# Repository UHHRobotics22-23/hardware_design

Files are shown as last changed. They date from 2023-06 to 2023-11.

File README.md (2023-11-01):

# Hardware Design
This repository contains the design files associated with the hardware mallet holder.
Further the firmware employed on the micro controller and a supporting calibration procedure script is contained.

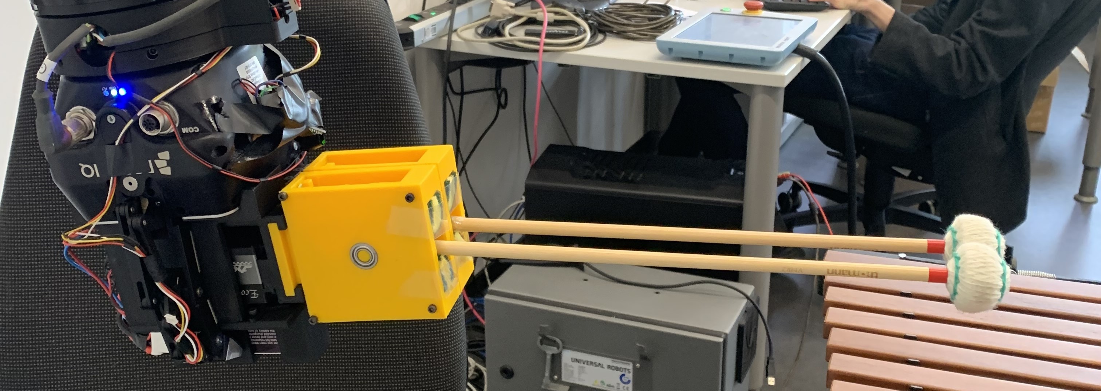
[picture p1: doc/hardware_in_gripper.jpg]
The mallet holder assembly in the gripper of the UR5

*The mallet holder assembly in the gripper of the UR5*

## Hardware Model Design
[OpenSCAD](https://openscad.org/) was used for the design of the 3D printable models.
Generally the designs can be separated into one and two mallet design, where the one mallet designs were the basis for the two mallet approaches.
All designs were created to be used in the [three finger gripper](https://robotiq.com/products/3-finger-adaptive-robot-gripper) employed as the end effector of the UR5.

### Two Mallet Designs
The two mallet designs are split into two categories, the servo controlled element and the attachments.
The servo controlled element contains all electronics and two mounting points for an attachment making the design more modular.
The attachments were then mounting the mallets, either with or without compliance.
#### Servo Controlled Element
All servo controlled elements have a standard "claw" element which the attachment modules can be slotted in to.

The first version of the servo controlled element [double_mallet_servo](design/two_mallet/double_mallet_servo/double_mallet_servo.scad) mainly tested the servo based control for the second mallet and the attachment mount.
[double_mallet_servo_compliant_full](design/two_mallet/double_mallet_servo/double_mallet_servo_compliant_full.scad) was used to generated STL models for a first URDF file with the [double_flex_v2](design/two_mallet/modular_attachments/double_flex_v2.scad) included.
Later versions were created in a more modular fashion.

[double_mallet_servo_UR5](design/two_mallet/double_mallet_servo/double_mallet_servo_UR5.scad) is the second iteration of the element. The length of the part was increased to allow the gripper to grab the device from the top.
Further the control and power electronics could be added to the back.
The top plate was changed to have indexing ridges to the gripper end effector of the UR5.
The [double_mallet_servo_UR5_battery](design/two_mallet/double_mallet_servo/double_mallet_servo_UR5_battery.scad) added a battery holder for the 2s lipo to the bottom plate.

#### Attachments
Three attachment design files exist for the two mallet holder.
All designs feature a standardized attachment mechanism to be added to the servo controlled element.

First the [static_mallet_attachment](design/two_mallet/modular_attachments/static_mallet_attachment.scad) is a simple static holder without added compliance generally used for testing.

In the final version the [double_flex_v2](design/two_mallet/modular_attachments/double_flex_v2.scad) has been used. It is based on the [double_flex_v1](design/one_mallet/double_flex_v1/mallet_mount_double_flex_v1.scad) and as such allows for flexibility in both directions using rubber bands. Two additional pieces of sponge were added at the top and bottom to dampen the movements.

[double_flex_v2_collision](design/two_mallet/modular_attachments/double_flex_v2_collision.scad) was not used.

### One Mallet Designs
The [rigid_base_version](design/one_mallet/rigid_base_version/rigid.scad) is the design used for playing with only one mallet. It features a simple holder and grabbing points for the end effector.

To generate louder sounds a compliant approach was devised.

[v1](design/one_mallet/v1/mallet_mount_v1.scad) is the first compliant design, featuring a one directional, up compliance when hitting the instrument. The compliance is achieved with rubber bands. [v2](design/one_mallet/v2/mallet_mount_v2.scad) is a minor iteration on the design using bearings and felt stickers to reduce noise.

The [double_flex_v1](design/one_mallet/double_flex_v1/mallet_mount_double_flex_v1.scad) allowed compliance into the up and down direction which showed improvements in the loudness of the instrument.

## Firmware
The firmware is implemented using the [Arduino](https://www.arduino.cc/) framework.
A [Raspberry Pi Pico W](https://www.raspberrypi.com/documentation/microcontrollers/raspberry-pi-pico.html) is used as the controller of the device.

### Protocol
The protocol used for the communication between ROS and the microcontroller is based on simple string commands. For both the wifi and serial version the same protocol is used.
Commands for the serial version have to be \n terminated.
The wifi version accepts both with and without

At first the ROS side is expected to request the bounds and resolution using the "l" command.
This allows for multiple devices with different bound to be used interchangeably though it could also be realized with config parameters on the ROS side.

The "p" command is used in the read phase of the hardware_interface (See [marimbabot_hardware](https://github.com/UHHRobotics22-23/marimbabot/tree/main/marimbabot_hardware)).

Lastly the "s" command allows the ROS side to give a integer valued command position to the microcontroller.

| Command | Response | Command Description | Response Description |
|---|---|---|---|
| s \<value> | ok, err_input_num, err_input_range | Commands the servo to move to the value <value> | Errors for invalid number formats or numbers out of range of the safety limits or ok for acknowledgement |
| p | p \<value> | Requests the current target value | Returns the current target value <value> |
| l | l <min_val> <max_val> <val_resolution> | Requests the limits of the device | Return the max and min value bounds and the resolution of the value parameter (0-res) |
| <invalid_command> | err_cmd | Any command other than the listed ones | Error code for and invalid / unknown command |

### Flavours
Two firmwares were written as a part of the development process.
First one using a usb serial connection and secondly one using a wifi network created by the microcontroller.

Both firmwares feature the min and max value at the top of the file.
These are the max and min angle the servo can safely be set to and depends on the real world alignment of the servo and the 3d print.
The values for each device are found in a manual testing project by sending manual "s" commands.
The resolution for both is set to 180 as the servo can cover 180°
Alternatively the resolution could be increased by using direct the [pwm millisecond control mode](https://www.arduino.cc/reference/en/libraries/servo/writemicroseconds/).

#### Wifi
The wifi firmware is found in the [mallet_play_servo_wifi](arduino_code/mallet_play_servo_wifi/mallet_play_servo_wifi.ino) project.

The SSID and the password of the generated network can be set at the top of the file and needs reflashing.
Further the port of the UDP server can be adjusted inside of the setup function.

Currently the defaults are:  
SSID: **Marimbabot_Mallet**  
PWD: **12345678**  
PORT: **8888**

Additional Note: In the libraries for the Raspberry Pi Pico W we found the Servo library to behave in unexpected ways which required a doubling of the input value to achieve the actually requested angle.

#### Serial
The serial firmware is found in the [mallet_play_servo](arduino_code/mallet_play_servo/mallet_play_servo.ino) project.

In the serial firmware the update frequency can be adjusted by changing the delay at the end of the loop.
The baud rate can be adjusted in the setup function. A high baud rate is needed to minimize the communication overhead.

## Electronics Design
The system was designed to be fully portable and battery powered to enable the usage in differing robotic arms.
Further the main used arms power budget was not able to power the device as the  end effector gripper exhausted this.

List of parts:
- Servo: [JX Servo CLS6336HV](http://jx-servo.com/en/Product/CORELESS1/HVcs/480.html)
- Battery: [CHHL 2S 2200mAh 30C](https://chinahobbyline.com/collections/cnhl-voltage-7-4v-2s-lipo-batteries/products/cnhl-2200mah-7-4v-2s-30c-lipo-battery-with-t-plug)
- DC Step Down: [LM2596](https://www.az-delivery.de/en/products/lm2596s-dc-dc-step-down-modul-1)
- Microcontroller: [Raspberry Pi Pico W](https://www.raspberrypi.com/documentation/microcontrollers/raspberry-pi-pico.html)
- A safety diode preventing current running back from a USB 5V supply

The system uses a 2s LIPO as its power source.
The servo is directly powered by the battery.
For the Raspberry Pi Pico W can only accept input voltages up to 5.5V.
A step down converter was used to step the 6-8V of the battery to 5V to safely power the microcontroller.

The full wiring diagram is shown in the following figure


## Hardware Calibration
The hardware calibration scripts are found in the [hardware_calibration](hardware_calibration) folder. The calibration is done by using a Azure Kinect depth camera in combination of color separation to find the 3d position of the red tapes on the mallets. The 3d coordinates are used to find the distance between the elements.
A mathematical model of the two mallet assembly is then used to find the expected opening angle from the distance. This angle is then compared to the commanded angle.

### How to use
First install the python dependencies using the [requirements.txt](hardware_calibration/requirements.txt) found in the hardware_calibration folder.

#### Setup
Use the azure kinect depth camera and connect it to the computer. A top down orientation onto the two mallet assembly indicated the best results. Clean the space of other red elements or cover them (like the red cables on the assembly).
Connect the computer to the Wifi sent out by the mallet assembly (the scripts use the raw control commands).

#### Data Collection
Two scripts are used for the measurement process.

First start [hardware_calibration.py](hardware_calibration/hardware_calibration.py).
This script uses the depth camera to measure the distance of the red tapes on the mallet.
The results are logged into a timestamped csv file (f"calibration-{time.time()}.csv").

Secondly start the [calibration_process.py](hardware_calibration/calibration_process.py).
This will generate the control input to the mallet holder and log to timestamp of each command.
One full sweep is run.
The data it logged into a timestamped csv file (f"calibration_pos-{time()}.csv").

After the sweep stop both scripts.

#### Data Preparation
To prepare the results remove all distance measurements before the first command value.
The analysis expects a continuous numberization of the meassurements.
The measured distance file also warrants careful examinations as the depth camera seems to have a few areas with bad accuracy.

#### Data Analysis
The data is analyzed using the Jupyter notebook [analyse_results.ipynb](hardware_calibration/analyse_results.ipynb).
To add new measurements extend the range operator in the 5th cell and run the notebook.
Especially the last graph gives a result about the angular offset for each commanded angle.

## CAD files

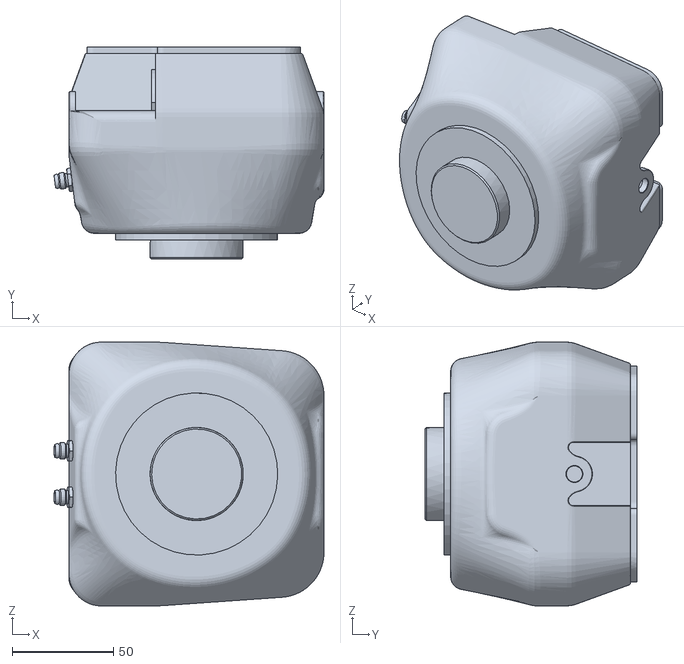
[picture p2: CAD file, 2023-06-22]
design/two_mallet/double_mallet_servo/palm_1.stl
133.2 x 104.8 x 130.2

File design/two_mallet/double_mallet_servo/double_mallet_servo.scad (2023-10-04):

/*
 * The first version of the two mallet holder servo controlled part
 */

$fa = 1;
$fs = 0.4;
/////////////////////////SERVO MODEL////////////////////////////
module servo(){
    color([0,0,1])
    difference (){
    union(){    
    rotate([90,0,90])//Servo Corpus
        cube([40, 39.5, 20]); 
        
    translate([0,40,8])//Screwholders
        cube([20,7.25,2.6]); 
    translate([0,-7.25,8])
        cube([20,7.25,2.6]);
    
    translate([10,10,-2]) //Drive shaft
        cylinder(h=3, r=6.5);
    translate([10,10,-5.5])
        cylinder(h=4, r=5.8/2);
        
    translate([10-3.5,-4.7,33])
        cube([7,8,5]);
        
    }
    ///////////Cutting///////////
    
    union(){ //Cut out Screwholes
    screwholes_servo();
    translate([20,40,0])
    rotate([0,0,180])
    screwholes_servo();
    }
}
  
}

// Screw Holder for connecting the servo
module screwholes_servo(){
     translate([0, 0, 7.9]) {
        translate([5, -7.25/2, 0]){
            cylinder(h=3, r=4.4/2);
            translate([-1.8,-4.8,0])
            cube([3.6, 4, 3]); 
        }
           translate([15, -7.25/2, 0]){
            cylinder(h=3, r=4.4/2);
            translate([-1.8,-4.8,0])
            cube([3.6, 4, 3]); 
        }
      
    }
}

// Module model for the drive shaft cross attachment used from the servo kit
module drive_shaft_attachment(){
    translate([-19,-19,0]){
        difference(){
            union(){
            
             translate([0,14.5,0])
                cube([38, 9, 2.77]); 
             translate([14.5,0,0])
                cube([9, 38, 2.77]); 
            translate([19,19,0])
                cylinder(h=5.4, r=4.4);   
                }
             union(){   
             translate([19,19,-00.1])//Driftshaft Clutch
                cylinder(h=6, r=5.8/2);
             translate([6,19,-00.1]) //Screwhole
                 cylinder(h=30, r=3/2);
              translate([32,19,-00.1])//Screwhole
                 cylinder(h=30, r=3/2);
              translate([19,32,-00.1])//Screwhole
                 cylinder(h=30, r=3/2);
              translate([19,6,-00.1])//Screwhole
                 cylinder(h=30, r=3/2);
             }
        }
    }
    
}

////////////////////////////////Servo Moveable Mallet//////////////////////////////
// Module with the servo casing and attachment claw
module mounting_plate(){
     color([0,1,0])
    difference(){
        union(){
                
          
               
            translate([0,-13.3,0]) //Sidewalls
                cube([35,6,60]);
             translate([0,40+7.5,0])
                cube([35,5,60]);
            
             translate([0,-10,54])//Topplate
                cube([35,60,6]);
            
            translate([20,-10,0])//inner structure
                cube([5,60,60]);
            
            translate([0,40,10.65])//counterpart screws
                cube([23,12,20]);
            translate([0,-12,10.65])
                cube([23,12,20]);
            
            translate([10,10,59]) //Axle Top
                cylinder(h=7, r=4);
                
            translate([35,-8.3,0]) // Claw for Mounting Plate
            rotate([0,0,180])
            claw();
        }
       union(){ ///////////Cutting///////////
          translate([15, -7.25/2, 9.9]) // Screwholes Mouting Plate
                cylinder(h=6, r=3/2);
          translate([5, -7.25/2, 9.9])
                cylinder(h=6, r=3/2);
           translate([20,40,0]){
               rotate([0,0,180]){
                    translate([15, -7.25/2, 9.9])
                        cylinder(h=6, r=3/2);
                    translate([5, -7.25/2, 9.9])
                        cylinder(h=6, r=3/2);
               }
           }
        translate([19,-5,40])//Cable channel
                cube([7,9,6]);
           
//        translate([0, -9.3, 0]){ // Screwholes for Mounting Plate
//            rotate([90,0,0]){
//                translate([30,5,0])
//                cylinder(h=5, r=3/2);
//                translate([5,5, 0])
//                cylinder(h=5, r=3/2);
//                translate([30,55, 0])
//                cylinder(h=5, r=3/2);
//                translate([5,55, 0])
//                cylinder(h=5, r=3/2);
//                translate([30,30, 0])
//                cylinder(h=5, r=3/2);
//                translate([5,30, 0])
//                cylinder(h=5, r=3/2);
//              
//            }
//        }
        
    
           
       }
    }
}


////////////////////////////////Housing # Main Structure//////////////////////////////
// Main structure for the housing with the claw for the fixed element
module housing(){
    difference(){
        union(){
            
            translate([-7,0,-6])//Bottomplate
                cube([77,110,6]);
            translate([35,0,-1]) //Frontplate Fix Mallet
                cube([35,6,68.4+1]);
       
            translate([70-6,20,-1]) //Sideplate Fix Mallet
                cube([6,60,68.4+1]);
            translate([70,5,8])
            rotate([0,0,180])
            claw();
        }
      
    
//         translate([35, +4, 8]){ // Screwholes for Mounting Plate
//            rotate([90,0,0]){
//                translate([30,5,0])
//                cylinder(h=6, r=3/2);
//                translate([5,5, 0])
//                cylinder(h=6, r=3/2);
//                translate([30,55, 0])
//                cylinder(h=6, r=3/2);
//                translate([5,55, 0])
//                cylinder(h=6, r=3/2);
//                translate([30,30, 0])
//                cylinder(h=6, r=3/2);
//                translate([5,30, 0])
//                cylinder(h=6, r=3/2);
//              
//            }
//        }
      screwholes();
        
}
}

// Module for the screwholes in the main housing 
module screwholes(){
     translate([-9,4.3,0]){
            
        translate([6,19,-4]) //Screwhole
                 cylinder(h=30, r=3/2);
        translate([32,19,-4])//Screwhole
                 cylinder(h=30, r=3/2);
        translate([19,32,-4])//Screwhole
                 cylinder(h=30, r=3/2);
        translate([19,6,-4])//Screwhole
                 cylinder(h=30, r=3/2);
         
        translate([40,80,-10])//Screwhole
                 countersunk();
        translate([40,80+22.86,-10])//Screwhole
               
                    countersunk();
                
                 
    }
     translate([-7,0,0-10]){ //Screwholes Sideplate Servo
             translate([3,35,0])
                countersunk();
             translate([3,65,0])
               countersunk();
            translate([3,95,0])
               countersunk();}
            translate([-10,0,68.4-6]){ //Screwholes Frontplate Fix Mallet
             translate([80-10,3,16])
                rotate([0,180,0])
                countersunk();
             translate([80-25,3,16])
               rotate([0,180,0])
                countersunk();
        }
         translate([-10,0,68.4-6]){ //Screwholes Sideplate Fix Mallet
             translate([77,35,16])
                rotate([0,180,])
                countersunk();
             translate([77,65,16])
               rotate([0,180,])
                countersunk();
         }

}

// Helper Module for counter sunk screw holes allowing for flush screws
module countersunk(){
    rotate([0,180,]){
        translate([0,0,-6]){
            translate([0,0,+1.67])
                cylinder(20,6/2,6/2);
            cylinder(  1.7,    3/2,    6/2, false);
            translate([0,0,-19]) 
                cylinder(30,3/2,3/2);
        }
    }
}
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

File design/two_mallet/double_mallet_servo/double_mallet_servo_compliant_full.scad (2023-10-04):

/*
 * Modified version of the double_mallet_servo with the flexible attachment included. For more documentation see the base files.
 */

$fa = 1;
$fs = 0.4;

side_wall_length = 90;
mallet_length = 365; // Hard Mallet
mallet_sphere_radius = 36.75/2;
mallet_sphere_height_h = 32/2;
axel_radius = 4;
side_wall_thickness = 5;
mallet_handle_radius=9.6/2;
side_wall_center_distance = mallet_handle_radius*2+1.5+side_wall_thickness/2;

module mallet() {
    cylinder(h=mallet_length+mallet_sphere_height_h, r=mallet_handle_radius);
    translate([0, 0, mallet_length+mallet_sphere_height_h])
        scale([1, 1, mallet_sphere_height_h / mallet_sphere_radius])
        sphere(r=mallet_sphere_radius, center=true);
}

module side_wall() {
    difference() {
        cube([side_wall_length, side_wall_length, side_wall_thickness], center=true);
        translate([0, 0, 0])
            cylinder(h=side_wall_thickness+1, r=8, center=true);
             translate([0, 0, side_wall_thickness-1])
            cylinder(h=side_wall_thickness, r=9, center=true);
    }

}

module side_wall_right() {
    difference() {
        side_wall();
        translate([0, 0, -side_wall_thickness-0.1])
            rotate([180, 0, 0])
            screw_holes(side_wall_thickness*2, 3, side_wall_length/2);  // 3mm width holes
    }
}

module side_wall_left() {
    wall_to_wall_distance = side_wall_center_distance*2-side_wall_thickness/2;
    side_wall();
    difference() {//Für die Schrauben
        union() {
            translate([side_wall_length/2-7.5, +40-2.5, wall_to_wall_distance/2])//Struktur Element fo stabilty Y Axes
                cube([15,15,wall_to_wall_distance],center=true);//Stopper
            translate([40-2.5, -side_wall_length/2+5+2.5, wall_to_wall_distance/2])
                cube([15,15,wall_to_wall_distance],center=true);//Struktur Element fo stabilty X Axes
            translate([-side_wall_length/2, -side_wall_length/2, 0])//Wall on Y Axes
                union() {
                    cube([side_wall_thickness, side_wall_length, wall_to_wall_distance]);
                    translate([side_wall_thickness+2, 10, wall_to_wall_distance/2+side_wall_thickness/4])
                        rubber_hook();
                 
                };
            translate([-side_wall_length/2, side_wall_length/2, 0])//Wall on X Axes
                union() {
                //rotate([0, 0, -90])
                    //cube([side_wall_thickness, side_wall_length, wall_to_wall_distance]);
                translate([7, -side_wall_thickness-2, wall_to_wall_distance/2+side_wall_thickness/4])
                        rotate([180,0, 0])
                        rubber_hook();
         
                };  
//         translate([-side_wall_length/2+7, (side_wall_length/2)-7, wall_to_wall_distance/2])//Wall on X Axes
//         rubber_attachment();   
     
        }
        translate([0, 0, wall_to_wall_distance])
            screw_holes(6, 3, side_wall_length/2);  // 6mm deep 3mm width holes
    }
}
module rubber_hook(){
    union(){
                        cube([10,5,5],center= true);    
                        translate([4,-2.5,0])
                            cube([5,10,5],center=true);
                        
                        }
    }

module mallet_car() {
    difference() {
        union() {
            cylinder(h=70, r=mallet_handle_radius*2, center=true);
            rotate([90, 0, 0])
                cylinder(h=2*(mallet_handle_radius*2+side_wall_thickness+2), r=axel_radius, center=true);
            rotate([90, 0, 0])
                cylinder(h=2*(mallet_handle_radius*2+1), r=5*2, center=true);
//            translate([0, 0, -37.5])
//                rotate([90, 0, 0])
//                rubber_attachment();
          translate([ -mallet_handle_radius*2,0,-27])
            rotate([90, 0, 0])
                rubber_attachment();
            translate([ mallet_handle_radius*2,0,-27])
            rotate([90, 0, 0])
                rubber_attachment();
        }
        translate([mallet_handle_radius, 0, 30])
            rotate([0, 90, 0])
                cylinder(h=mallet_handle_radius*2, r=3/2,center = true);
        translate([mallet_handle_radius, 0, -15])
            rotate([0, 90, 0])
                cylinder(h=mallet_handle_radius*2, r=3/2,center = true);
        
        translate([0, 0, -30])
            scale(1.07)
            mallet();
    }
    
}

module rubber_attachment() {
    rotate_extrude(angle=360) {
        translate([4, 0, 0])
            circle(r=1.5);
    }
}

module mallet_holder() {
    translate([0, side_wall_center_distance, 0])
        rotate([90, 0, 0])
            side_wall_right();

    translate([0, -side_wall_center_distance, 0])
        rotate([-90, 0, 0])
        side_wall_left();

    rotate([0, 90, 0]){
        mallet_car();
        translate([0, 0, -30])
        mallet();
    }
    translate([-56.8, +35/2, -25])
        rotate([0, 0, -90])
            attachment();
}

module screw_holes(depth, width, corners) {
    posVal = corners - side_wall_thickness / 2;
    translate([0, 0, -depth+0.001]) {
        translate([-posVal, -posVal, 0])
            cylinder(h=depth, r=width/2);
        translate([-posVal, posVal, 0])
            cylinder(h=depth, r=width/2);
        translate([posVal-5, posVal-5, 0])
            cylinder(h=depth, r=width/2);
        translate([posVal-5, -posVal+5, 0])
            cylinder(h=depth, r=width/2);
        
//        translate([side_wall_length/2-7.5, +40-2.5, wall_to_wall_distance/2])
//            cylinder(h=depth, r=width/2);
        
//        translate([40-2.5, -side_wall_length/2+5+2.5, wall_to_wall_distance/2])
//            cylinder(h=depth, r=width/2);
    }
}

module attachment() {
    difference() {
        union() {
            cube([33.5, 6, 50]);
            translate([6.5, 6, 5+0.15])
                cube([27, 6.01, 40-0.3]);
        }
        union() {
            translate([35/2, 6/2, 3.5-0.001])
                cylinder(h=7, r=3/2, center=true);
            translate([35/2, 6/2, 46.5+0.001])
                cylinder(h=7, r=3/2, center=true);
        }
    }
}


/////////////////////////SERVO MODEL////////////////////////////
module servo(){
    color([0,0,1])
    difference (){
    union(){    
    rotate([90,0,90])//Servo Corpus
        cube([40, 39.5, 20]); 
    
    translate([0,40,8])//Screwholders
        cube([20,7.25,2.6]); 
    translate([0,-7.25,8])
        cube([20,7.25,2.6]);
    
    translate([10,10,-2]) //Drive shaft
        cylinder(h=3, r=6.5);
    translate([10,10,-5.5])
        cylinder(h=4, r=5.8/2);
        
    translate([10-3.5,-4.7,33])
        cube([7,8,5]);
        
    }
    ///////////Cutting///////////
    
    union(){ //Cut out Screwholes
    screwholes_servo();
    translate([20,40,0])
    rotate([0,0,180])
    screwholes_servo();
    }
}
  
}

module screwholes_servo(){
     translate([0, 0, 7.9]) {
        translate([5, -7.25/2, 0]){
            cylinder(h=3, r=4.4/2);
            translate([-1.8,-4.8,0])
            cube([3.6, 4, 3]); 
        }
           translate([15, -7.25/2, 0]){
            cylinder(h=3, r=4.4/2);
            translate([-1.8,-4.8,0])
            cube([3.6, 4, 3]); 
        }
      
    }
}

module drive_shaft_attachment(){
    translate([-19,-19,0]){
        difference(){
            union(){
            
             translate([0,14.5,0])
                cube([38, 9, 2.77]); 
             translate([14.5,0,0])
                cube([9, 38, 2.77]); 
            translate([19,19,0])
                cylinder(h=5.4, r=4.4);   
                }
             union(){   
             translate([19,19,-00.1])//Driftshaft Clutch
                cylinder(h=6, r=5.8/2);
             translate([6,19,-00.1]) //Screwhole
                 cylinder(h=30, r=3/2);
              translate([32,19,-00.1])//Screwhole
                 cylinder(h=30, r=3/2);
              translate([19,32,-00.1])//Screwhole
                 cylinder(h=30, r=3/2);
              translate([19,6,-00.1])//Screwhole
                 cylinder(h=30, r=3/2);
             }
        }
    }
    
}
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

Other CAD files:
design/two_mallet/double_mallet_servo/double_mallet_servo_UR5.scad
design/two_mallet/double_mallet_servo/double_mallet_servo_UR5_battery.scad
design/one_mallet/double_flex_v1/mallet_mount_double_flex_v1.scad
design/one_mallet/rigid_base_version/rigid.scad
design/one_mallet/v1/mallet_mount_v1.scad
design/one_mallet/v2/mallet_mount_v2.scad
design/two_mallet/modular_attachments/double_flex_v2.scad
design/two_mallet/modular_attachments/double_flex_v2_collision.scad
design/two_mallet/modular_attachments/static_mallet_attachment.scad
double_flex_v1/mallet_mount_double_flex_v1.scad

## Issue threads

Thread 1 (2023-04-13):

Create URDF for 2 mallet grabber

Juphex, 2023-04-13:
https://github.com/UHHRobotics22-23/marimbabot/tree/feature/two_mallet_xacro

Juphex, 2023-04-13:
@cvhex @ateRstones  fyi

ateRstones, 2023-05-25:
Add a mechanism for loading different attachments

Closed 2023-05-25.

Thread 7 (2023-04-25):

Design a mallet holder with around 5° of compliance

cvhex, 2023-04-25:
As it turns out, not as much comliance is needed as originally thought. Therefore, it is now necessary to construct a malletholder that has much less comliance.

cvhex, 2023-04-25:
A prototype is ready and will probably go to print on Wednesday. The reduced comliance is to be realized primarily via stronger rubber bands in order to avoid additional noise due to impacts.

Closed 2023-05-25.

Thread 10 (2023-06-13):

Buy batteries for a better two mallet assembly

ateRstones, 2023-06-13:

ateRstones, 2023-06-13:
I already bought 2s lipos, plugs to solder to and a charger.
But looks like the charger will take time to arrive (10th of July)
The other things should be here faster

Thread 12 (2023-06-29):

Calibration of the two mallet assembly with actual measurements

ateRstones, 2023-06-29:
https://github.com/UHHRobotics22-23/hardware_design/pull/16

ateRstones, 2023-08-10:
Could measure distance of red tape on mallets -> could lead to perspective error
Also need math model for the system (triangle intersect with off axis rotation

also could use april tags for 3d position

Closed 2023-10-02.

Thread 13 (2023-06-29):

Add a mounting point for the battery and power converter in the two mallet assembly

ateRstones, 2023-06-29:
We might consider a mount at the bottom with a battery mounted rotated on the slimmer side

Closed 2023-07-06.

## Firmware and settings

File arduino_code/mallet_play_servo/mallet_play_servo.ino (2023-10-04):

/*
 * This file the serial connection based firmware for the two mallet holder.
 * It is intended to be used with a Raspberry PI Pico, not the Pico W as the Servo library of the Pico W behaves differently
 */
#include <Servo.h>

int DELAY_MS = 5;         // A delay controling the maximum update rate of the loop in ms
int STEP_INCREASE = 1;    // Not used

int MAX_VALUE = 180;      // Max control value not creating collisions in the assembly
int MIN_VALUE = 0;        // Min control value not creating collisions in the assembly
int RESOLUTION = 180;     // Resolution of the control value. 180 as the standard write function for servos is used.


String input;             // Input "buffer" from the serial connection
String input_number;      // Input substring containing the command value number
Servo malletServo;        // Servo Object

int targetPos = 97;       // target position. Used if slowly approaching the target
int pos = 97;             // Current set position of the servo

void setup() {
  Serial.begin(115200);
  malletServo.attach(2);  // Servo is controlled from pin 2
  malletServo.write(pos);
}

void loop() {
  // If serial messages are present or we reached the target position
  if(pos == targetPos || Serial.available() > 0) {
    // Serial.println("Awaiting new command");

    // Wait if there are no messages available
    while(Serial.available() == 0) {
      delay(DELAY_MS);      
    }

    input = Serial.readStringUntil('\n');
    input.trim();

    // Command for setting the position of the servo
    if(input.startsWith("s ")) {
      input_number = input.substring(2);
      long servoInput = input_number.toInt();
      // Check if the string was actually a valid number
      if(!check_input_number_string() || servoInput < 0) {
        Serial.println("err_input_num");
      } else {
        // Check if the input is within the valid range
        if(((int) servoInput) < MIN_VALUE || ((int) servoInput) > MAX_VALUE) {
          Serial.println("err_input_range");
        } else {
          targetPos = (int) servoInput;
          Serial.println("ok");
        }
      }
    }

    // Command for getting the current position of the servo
    else if(input.startsWith("p")) {
      Serial.print("p ");
      Serial.println(pos); 
    }

    // Command for getting the limits and resolution of the controller
    else if(input.startsWith("l")) {
      Serial.print("l ");
      Serial.print(MIN_VALUE);
      Serial.print(" ");
      Serial.print(MAX_VALUE);
      Serial.print(" ");
      Serial.println(RESOLUTION);
    }

    else {
      Serial.println("err_cmd");
    }
  }

  // Set to pos to targetPos immediately. Could readd lower code later for velocity constraining
  pos = targetPos;

  // if(pos < targetPos) {
  //   pos += min(STEP_INCREASE, targetPos - pos);
  // } else if(pos > targetPos) {
  //   pos -= min(STEP_INCREASE, pos - targetPos);
  // }

  malletServo.write(pos);
  
  delay(DELAY_MS);
}

// Simple function to check if all characters of the number string are valid numbers.
bool check_input_number_string() {
  for(int i = 0; i < input_number.length(); i++) {
    char c = input_number.charAt(i);
    if(c < '0' || c > '9') {
      return false;
    }
  }

  return true;
}

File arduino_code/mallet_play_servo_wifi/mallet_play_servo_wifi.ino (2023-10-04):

/**
 * The wifi based firmware for the two mallet servo controlled assembly.
 * Intended to be used with a Raspberry Pi Pico W as the code contains a workaround for the behaviour of the Servo library.
 */
#include <WiFi.h>
#include <WiFiClient.h>
#include <Servo.h>
#include <iostream>
#include <string>

int DELAY_MS = 5;       // Not used
int STEP_INCREASE = 1;  // Not used
int MAX_VALUE = 140;    // Max control value not creating collisions in the assembly
int MIN_VALUE = 70;     // Min control value not creating collisions in the assembly
int RESOLUTION = 180;   // Resolution of the control value. 180 as the standard write function for servos is used.

String input;           // Input "buffer" from the serial connection
String input_number;    // Input substring containing the command value number
String l_send;          // Send string "buffer" for l command
String p_send;          // Send string "buffer" for p command
String s_send;          // Send string "buffer" for s command
String err_send;        // Send string "buffer" for unknown commands

Servo malletServo;      // Servo Object

int targetPos = 140;    // target position. Used if slowly approaching the target
int pos = 140;          // target position. Used if slowly approaching the target
char packetBuffer[255]; // Buffer for udp packet data
// WIFI Setup
const char* ssid = "Marimbabot_Mallet"; // WIFI SSID
const char* password = "12345678";      // WIFI Password

// Set the IP address and port number for the server
// IP Adress: '192.168.42.1'
const uint16_t serverPort = 80;   // Not used
WiFiUDP udp;      // UDP Server

void setup() {
  Serial.begin(115200);
  malletServo.attach(2);    // Servo is controlled from pin 2
  malletServo.write(pos);

  // Connect to Wi-Fi network
  WiFi.softAP(ssid, password);
  Serial.println("Access Point created");

  // Start the server
  udp.begin(8888);          // UDP Server on port 8888
  Serial.print("Server listening on ");
}
void loop() {
  memset(packetBuffer, -1, 255);
  int packetSize = udp.parsePacket();
  if(pos == targetPos || packetSize > 0) {
    int len = udp.read(packetBuffer, 255);

    if (len > 0) {

      // Command for setting the position of the servo
      if(packetBuffer[0]=='s') {
        input_number = "";
        // Checking the amount of digits sent by the client
        if(packetBuffer[4] >= '0' && packetBuffer[4] <= '9') {
          input_number.concat(packetBuffer[2]);
          input_number.concat(packetBuffer[3]);
          input_number.concat(packetBuffer[4]);
        }
        else if(packetBuffer[3] >= '0' && packetBuffer[3] <= '9') {
          input_number.concat(packetBuffer[2]);
          input_number.concat(packetBuffer[3]);
        }
        else{
          input_number.concat(packetBuffer[2]);
        }

      // Converting to int and checking validity of number
      long servoInput = input_number.toInt();
      if(servoInput < 0) {
        Serial.println("err_input_num");
        udp_sender("err_input_num");
        }
      else {
        if(((int) servoInput) < MIN_VALUE || ((int) servoInput) > MAX_VALUE) {
          Serial.println("err_input_range");
          udp_sender("err_input_range");
        } 
        else {
          targetPos = input_number.toInt();
          udp_sender("ok");
          
        }
      }

      }

      // Command for getting the current position of the servo
      //The actual postion is send to ROS
      else if (packetBuffer[0]=='p') {
        p_send ="p ";
        p_send.concat(pos);
        udp_sender(p_send);
      }

      // Command for getting the limits and resolution of the controller
      else if(packetBuffer[0]=='l') {
        l_send ="l ";
        l_send.concat(MIN_VALUE);
        l_send.concat(" ");
        l_send.concat(MAX_VALUE);
        l_send.concat(" ");
        l_send.concat(RESOLUTION);
        
        udp_sender(l_send);
     
      }

      else {
        err_send ="err_cmd";
        udp_sender(err_send);
        Serial.println("err_cmd");
      }
    }
  }
  
  // Set to pos to targetPos immediately. Could add velocity constraining by limiting with a iteration based step
  pos = targetPos;

  // Ignore below command, was written after hours of debugging. But a two times multiplyer is needed
  // Ok, hear me out. We need to double scale this because someone in the pico w servo library made a oopsi
  malletServo.write((pos - 140) * 2 + 140);
}

// Simple helper function to send a udp reply
void udp_sender(String sender_message){

  udp.beginPacket(udp.remoteIP(), udp.remotePort());
  udp.write(sender_message.c_str());
  udp.endPacket();
}

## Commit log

2023-01-12 Added current state of v1
    [mallet_mount_v1.scad]
2023-01-12 Added holes for screws
    [mallet_mount_v1.scad]
2023-01-17 Small adjustments
    [mallet_mount_v1.scad]
2023-01-19 Implementing many first small changes for v2
    [mallet_mount_v2.scad]
2023-01-23 A first iteration of a rigid version
    [rigid.scad]
2023-01-23 Changes for V2 are implemented
    [mallet_mount_v2.scad]
2023-01-24 A first try to make the mallet holder without a stopper
    [mallet_mount_double_flex_v1.scad]
2023-01-26 Small adjustments for v2 such that the mallet fits better + rubber holder doesn't collide with the stopper
    [mallet_mount_v2.scad]
2023-01-26 optimized double flex version
    [mallet_mount_double_flex_v1.scad]
2023-02-27 Changed the rigid version to fit the gripper more
    [rigid.scad]
2023-03-09 First Approach to integrate the Servo into OpenSCAD. Simulated the Servo and build the housing arounf it
    [double_mallet_servo.scad]
2023-03-09 The Housing for the Servo is quite far. We still need to think about how to print.
    [double_mallet_servo.scad]
2023-03-16 Adding simple code to control the servo
2023-03-17 Furture Improvements on the Servo Housing
    [double_mallet_servo.scad]
2023-03-30 Arduino Code changed for current prototype
    [rigid.scad]
2023-03-31 First modular attachment: static mallet holder
    [static_mallet_attachment.scad]
2023-04-05 Added servo safety bounds
2023-04-20 Working state of arduino code with ros_control
2023-04-20 Added feedback command and faster responses in arduino code
2023-04-24 I Added a double flex Malletholder with an attachment Plate.
    [double_flex_v2.scad, mallet_mount_v2.scad]
2023-04-24 cleaning and file movement
    [double_flex_v2.scad]
2023-04-24 for 3D print optimized
    [double_flex_v2.scad]
2023-04-27 Colision Model created for double flex mallet holder
    [double_flex_v2_collision.scad]
2023-05-11 I Added a Version for the Pico W where it is possible to access without physical connection
    [double_flex_v2.scad]
2023-05-11 Added full two mallet compliant model for urdf
    [double_mallet_servo_compliant_full.scad]
2023-05-23 Changed the Code of the Pico, to controll it over a Wifi UDP Connection
2023-05-25 Changed the size of the two mallet approach and optimized the design
    [double_flex_v2.scad, double_mallet_servo.scad]
2023-05-30 Modification for UR5
    [double_mallet_servo_UR5.scad, palm_1.stl]
2023-06-15 Added Arduino Pico W with Wifi function
    [double_mallet_servo.scad]
2023-06-15 optimzing arduino code
2023-06-15 Optimized the arduino code
2023-06-22 bugfixing for chekcing if number with 1,2 or 3 digits
    [mallet_play_servo_wifi.ino]
2023-07-03 Added holding brackets for the battery
    [double_mallet_servo_UR5_battery.scad]
2023-07-06 Fixed limits in serial controlled servo
    [double_mallet_servo_UR5_battery.scad]
2023-07-13 modified the arduino code wifi, cleanup and optimization
2023-07-13 We had some problems with the servo angle. There is a bug in the software for the pico w.
    [mallet_play_servo.ino, mallet_play_servo_wifi.ino]
2023-08-21 Moved hardware calibration components from marimbabot to the hardware repo
    [calibration-distance-1-cleaned.csv, calibration-distance-2-cleaned.csv, calibration-distance-3-cleaned.csv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]
2023-10-02 Added a readme for the calibration process
2023-10-04 Restructuring and starting to extend the readme file
    [double_flex_v2.scad, double_flex_v2_collision.scad, double_mallet_servo.scad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]
2023-10-04 Adding the circuit svg
2023-10-04 Adding code documentation
    [double_flex_v2.scad, double_flex_v2_collision.scad, double_mallet_servo.scad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]
2023-10-17 Fixed gripper references
